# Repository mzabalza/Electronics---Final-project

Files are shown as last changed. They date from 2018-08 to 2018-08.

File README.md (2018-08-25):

# Electronics-Final_project
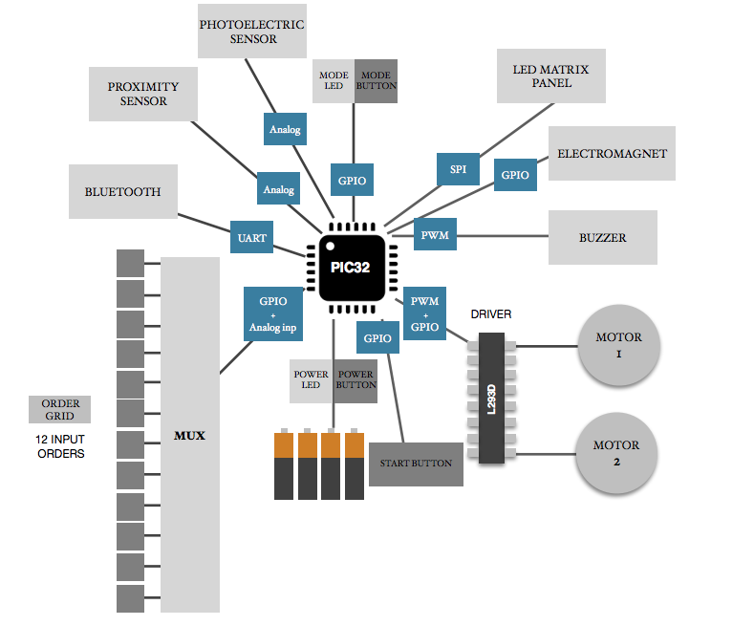
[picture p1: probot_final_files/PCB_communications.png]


## 1. Probot_final_files
- Project description pdf(Probot_memory_v4).
- Bill of materials (BOM).
- Datasheets of every electronic component.
- Gerber files.
- Altium schematics of project.

## 2. Test_components
- PIC32MX340F256H datasheet.
- C code programms of every functioanlity:
  - Motor driver
  - Mux
  - Proximity sensor
  - Bluetooth
  - LDR
  - Led Matrix

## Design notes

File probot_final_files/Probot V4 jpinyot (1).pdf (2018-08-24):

# 42 ELECTRONICS

# Technical Reference

Authors: Mikel Zabalza, Josep Pinyot, Jaume Garcia

08 03 2018

Version 1.4

# PROBOT

# CONTENTS

### 1 Introduction

### 2 Block Diagram

### 3 Instruction manual

### 4 Components

4.0 Component table
4.1 PIC32MX1
4.2 Proximity sensor
4.3 Photoelectric sensor
4.4 Order grid
4.5 Motor
4.5.1 Motor Driver
4.6 LED
4.7 Electromagnet
4.8 Display panel
4.9 Buzzer
4.10 Bluetooth
4.11 Battery
4.12 Mode Selector
4.13 Robot structure

### 5 Electric Consumption

### 6 Protocols

6.1 PWM
6.2 GPIO
6.3 SPI
6.4 UART
6.5 Motors
6.6 Analog

# 1. INTRODUCTION

Probot is a programable robot, able to make different moves and actions, Its an introduction to robotics and programming, making it more accessible for the youngest audience .This 2-wheel-driven robot is designed to be configured through visual programming.

## 1.1 MAIN UTILITIES

Perform a series of movements pre introduced by the user through an APP or through a physic panel using specific pieces that represent the movements: go forward, go backward, turn left and turn right. There will be too more specific pieces representing, velocity, performing time for a movement, reproduce sounds and degrees of turn.

Apart from the main utilities our project will be able to detect colours from the floor and detect collisions allowing the user create labyrinths himself for solve using the commands and treating the cases of collision and colour error as if the user would have failed, and it could take little metal objects too using an electromagnet.

It could save specific patrons in memory for perform complex and varied sets of movements.

The robot contains a led panel to be able to show the actual movements that it is performing among other esthetics things as messages, expresions, faces …

## 1.2 GOAL

The aim of this project is to make a toy in a computational thinking concept, So that its users can develop skills such us:

- Develop programs to complete certain tasks (go through a labyrinth, pick up objects…)
- Understand the execution of the selected program
- Learn through error and predict what a program will do.
- Evaluate and refine a simple program.

# 2. INSTRUCTION MANUAL

Probot is an introduction to robotics and programming for the youngest audience .The robot is designed to execute a set of action through an app, that communicates with the robot via bluetooth, and a grid of different pieces witch you can choose to run specific actions.

The user is able to change between the two possibles inputs with the “mode selection” button, through the colour of the LED the user will know the selected input (blue for bluetooth and red for the grid orders).

## 2.1 CONFIGURATION WITH THE GRID

The grid is the main part of Probot, it is located at the top of the robot to facilitate the interaction. To run Probot with the grid make sure the “mode selection” LED is red, if not the user can change from bluetooth to grid mode pressing the button next to it (the “mode selection” button).

Once Probot is set in grid mode, the user can place the set of piece he want to move the robot, thanks to the sensor located in front of the robot it will never crash.

The different pieces the user can use are:

GO FORDWARE: to make the robot move forward.

GO BACKWARDS: to make the robot move backwards.

TURN LEFT: to make the robot turn left.

TURN RIGHT: to make the robot turn right.

POWER IMAN: to power the electromagnet located down the robot.

STOP IMAN: to stop the electromagnet located down the robot.

POTENTIOMETER: this piece consist of a simple potentiometer, that the user can place it right after the command pieces to change some values of the action (for FORDWARE and BACKWARDS pieces will change the distance to travel and for TURN pieces will change the angel). Also the user can place one POTENTIOMETER in the first place of the grid to change the speed of all the actions.

GUIDE ME: this pieces is designed to help the youngest play with Probot, helped with the distance sensor Probot will set automatically the distance and the angle to avoid collision, when it moves and turns respectively.

## 2.2 CONFIGURATION WITH THE APP

To run Probot with the app make sure the “mode selection” LED is blue, if not the user can change from grid to bluetooth mode pressing the button next to it (the “mode selection” button).

The Probot app is a easy to use interface with similar options as the grid, the main different with the grid are the limited places were the user can place the pieces in the grid and the memory option.

The memory option is a interesting option when the user find a pattern of pieces that runs the robot without crashing. When the user wants to save a pattern he needs to press the “memory” button on the app, also the user will be able to name the pattern. When the user wants to recover the pattern he will need to press the “recover” button and select the wanted pattern from the menu.

### 2.3 INTERACTIVE PARTS

Probot will be able to interact directly with the user with the LED panel and the buzzer. Both are build not just to facility and improve the experience with the robot, also thous parts will hep the user to know interesting things about the patterns.

LED PANEL: It will help the user to know the step of his pattern the robot has crashed, showing the number of the piece.

PUZZER: The buzzer will help the user emitting sounds when it crash and a simple music when he found a pattern that runs the Probot without crashing.

# 3. BLOCK DIAGRAM

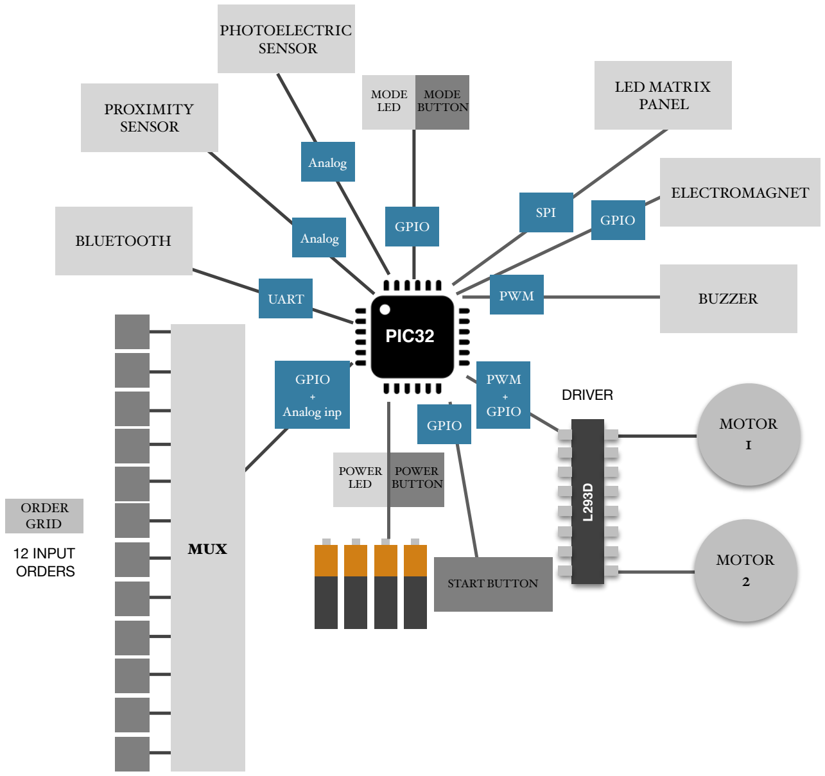
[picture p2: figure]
12 INPUT ORDERS; MOTOR 1; MOTOR 2; PIC32; DRIVER; ORDER GRID; BLUETOOTH; PROXIMITY SENSOR; BUZZER; LED MATRIX PANEL; POWER LED; UART; PWM +; GPIO; GPIO + Analog inp; POWER BUTTON; MODE LED; MODE BUTTON; MUX; START BUTTON; ELECTROMAGNET; PWM; SPI; Analog; PHOTOELECTRIC SENSOR

COMPONENT

PROTOCOL

# 4. COMPONENTS

## 4.1 COMPONENT TABLE

Component | Uds | Manufactu rer | M. Reference | Supplier | S. Reference | Price (EUR)
Microcontroller | 1 | Microchip | PIC32MX270F256 D-50I/PT | Farnell | 2449081 | 4.46
Proximity sensor | 1 | SHARP | GP2Y0A41SK0F | Farnell | 1618431 | 15
Female PIN sensor | 1 | Pololu | 3-Pin Female JST PH-style | Exp-tech | - | 0.82
Buzzer | 1 | Pro-signal | ABT-414-RC | Farnell | 2098836 | 1.55
Drive Motor | 1 | Texas Instruments | L293DNE | Farnell | 1470423 | 1.78
Analog MUX | 1 | Texas instruments | CD74HC4067SM96 | Farnell | 1601157 | 0.4
Led matrix | 1 | Kingbright | TA08-81GWA | Farnell | 2290396 | 6.15
Shift Register | 2 | Texas Instruments | CD74HC164M | Farnell | 1103161 | 0.589 x 2 = 1.17
Bluetooth module | 1 | MICROCHIP | RN4020-V/RM | Farnell | 2442930 | 9,38
Photoelectric sensor | 1 | ADVANCED PHOTONIX | NORPS-12 | Farnell | 327700 | 3.18
Potentiometer | 1 | BOURNS | 3362P-1-103LF | Farnell | 9354391 | 1
Mode Switch | 2 | NKK switches | SS12SDP2 | Farnell | 1524325 | 0.05 x 2 = 0.1

## 4.1 MICROCONTROLLER

PIC32MX270F256D-50I/PT

Fabr. Ref | PIC32MX270F256D-50I/PT
Farnell Code | 2449081
Frecuency: | 50MHz
Pins: | 44 where 34 are I/O.
Interfaces: | UART, SPI, I²C, I²S, USB
RAM: | 64KB
Memory size: | 256KB
Consume (50 Mhz) | 25mA
USED PINS

USED PINS:

I = Input | O = Output | CO = Compare Output
CONNECTED COMPONENT | PIN | FUNCTION
POWER | 1 | RB9 – I
MODE | 2, 3, 4 | RC6 – I/ RC7 – O/ RC8 – I
GRID ON | 5 | RC9 – O
PROXIMITY SENSOR | 11 | AN11 – I
GRID | 36, 30, 31, 32, 33, 34 | AN12 — I / RA2 — O / RA3 — O / RA8 — O / RB4 — O / RA4 — O
DECODER GRID | 8, 9 | RB10 – O / RB11 – O
MTR DRIV PULSE | 19, 20 | RPA0 – CO / RPA1 – CO
MTR DRIV MTR1 | 21, 22 | RB0 – O/ RB1 – O
MTR DRIV MTR2 | 23, 24 | RB2 – O/ RB3 – O
ELECTROMAGNET | 27 | RC2 — O
MATRIX LED | 14, 41, 43, 44 | SCK / RPB5 — SPI / RPB7 — SPI / RPB8 — SPI
BUZZER | 15 | RPB15 – CO
BLUETOOTH | 12, 13, 25, 26 | RA10 – O / RA7 – O / RPC0 – Rx / RPC1 – Tx

### 4.2 PROXIMITY SENSOR

The infrared proximity sensor will detect how far away an object is, the PIC32 micro controller will interpret the input and generate an order. Example: stop the motors before hitting an obstacle.

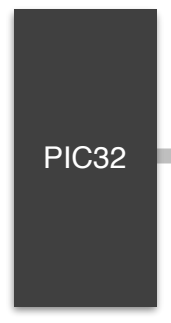
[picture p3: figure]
PIC32

The sensor will output an analog voltage depending how far away an object is from the sensor. It will be connected to the micro controller using the Analog to Digital converter pin.

SNS-US020 Ultrasonic Sensor

- Manufacturer SHARP
- Supplier Farnell
- Manufacturer Reference GP2Y0A41SK0F
- Supplier Reference 1618431
- Range 4 to 30cm
- Power supply 4.5 to 5.5 V
- Analog voltage output 0.4V
- Consumption 30 mA
- Price 7.8 EUR

The sensor needs a 3 pin adapter to be able to connect it to the PCB.

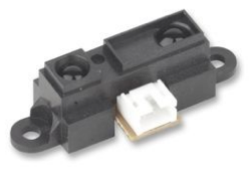
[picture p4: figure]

The 3-Pin Female JST PH-Style Cable has been selected for this purpose

3-Pin Female JST PH-Style Cable

- Manufacturer Pololu
- Supplier exp-tech
- Price 0.82 EUR

RA0/VA0

+5V

Vo | Vcc
OUT

GND

The graphic below taken from the data sheet shows how the voltage output from the sensors varies with the distance detected. With distances below 4cm we could get repeated voltages and above 30 cm, they are not conclusive.
Considering this we will able to assign the different voltage inputs between 0, 4 and 3 V to its corresponding distance, in our PIC32. However we will set 0 and 5V as reference voltages. The digital value is calculated based on following equation.

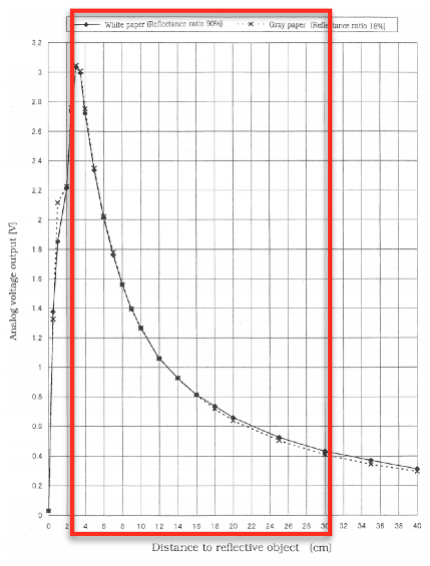
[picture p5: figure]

Interfacing to the microcontrollers is straightforward. The sensor will output a single analog output voltage (OUT) connected to an analog-to-digital converter for taking distance measurements. The 10-bit ADC pin of the PIC provides readings from 0 to 1023 as the input voltage rises from 0 to Vdd (5V).
The sensor automatically updates the output approximately every 16 ms.

### 4.3 PHOTOELECTRIC SENSOR

The LDR will be used with a RGB LED to detect colours. Measuring the LED’s light reflected in the surface we want measure having like that 3 measures one for RED, another for GREEN and one last for BLUE, with those three measures we can determinate a colour.

For the LDR one side of the sensor will be connected to the power supply while the other will be connected to an analogical input pin of the microcontroller. The analog input will be connected to a pull-down resistor to ground.

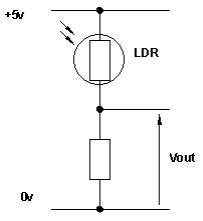
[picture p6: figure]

we will use the model LDR CdS PHOTO CELL from Farnell with the specifications:

LDR CdS PHOTO CELL

- Manufacturer ADVANCED PHOTONIX
- Supplier Farnell
- Supplier Reference NORPS’12
- Supplier Reference 327700
- Darkness resistance 1 Mohm
- Darkness resistance 100 Kohm

RGB LED

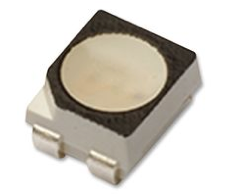
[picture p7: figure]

- Manufacturer BROADCOM LIMITED
- Supplier Farnell
- Supplier Reference ASMB-MTB0-0A3A2
- Supplier Reference 2401105
- Direct Tension R 2.1V / G 3.1V / B 3.1V
- Direct Current R 20mA / G 20mA / B 20mA

For the RGB LED we have 4 pins:

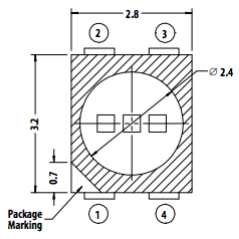
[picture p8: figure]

The anode will be connected to GND and the others connected to a resistor and a digital pin.

### 4.4 ORDER GRID

As explained in the instruction manual, the robot could be programmed plugging some pieces directly into the car. So the car is going to have 16 holes available for 10 different types of pieces(each piece representing an order, such us, go straight/backwards, turn left-right, activate magnet…). A 16-Channel Analog Multiplexer has been selected to connect 16 inputs of the order grid with the micro controller.

The multiplexer is a combinational circuit device that selects one of N inputs and provides it on its output. We can determine which input should be passed to the output trough a number of digital inputs called select lines. If there are n select lines, then the maximum input lines are 2^n.
In this case, with a multiplexer of 16 analog inputs we need 4 select lines. The 4 select lines will be General-purpose input/output (GPIO), configured as digital outputs from our PIC32. The figure below shows how the combination of all 4 select lines will allow us to select the desired analog output (L= Low, H = High):

The selected multiplexer has also an ENABLE input, which has to to be activated to perform the multiplexer operation. This will be also an general purpose input/output (GPIO) from the PIC32. This integrated circuit has active LOW ENABLE and the 4 select lines as input and gives complementary outputs.

S1 INPUT | S2 INPUT | S3 INPUT | S4 INPUT | E ENABLE | OUTPUT
L | L | L | L | L | D0
L | L | L | H | L | D1
L | L | H | L | L | D2
L | L | H | H | L | D3
L | H | L | L | L | D4
L | H | L | H | L | D5
L | H | H | L | L | D6
L | H | H | H | L | D7
H | L | L | L | L | D8
H | L | L | H | L | D9
H | L | H | L | L | D10
H | L | H | H | L | D11
H | H | L | L | L | D12
H | H | L | H | L | D13
H | H | H | L | L | D14
H | H | H | H | L | D15

The image below shows the scheme of the input grid - mix - PIC32. The order pieces are represented with the green boxes.

un

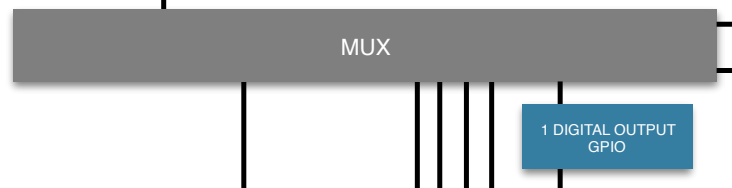
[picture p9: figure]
MUX; 1 DIGITAL OUTPUT GPIO

This is the selected MUX:

16 :1 Analog Multiplexer

- Manufacturer TEXAS INSTRUMENTS
- Supplier Farnell
- Manufacturer Reference CD74HC4067SM96
- Supplier Reference 1601157
- Power supply 2 to 6 V
- PINS 24

The Analog input received by the PIC32 will be a voltage value between 0 and 3.3 V. The PIC receive this input through its 10 - bit analog to digital conversion input (ADC). This pin is able to read 1024 different values between voltage 0 and 3.3 V. In this project there will be just 10 different cases, representing 10 different inputs (10 different R2).

ANALOG
INPUT (ADC)

4 DIGITAL OUTPUT
GPIO

+5V

Vcc

Gnd

Selecting a value of R1 (50 Ohm) and combining different input values of R2, we obtain different voltage outputs, as it is shown in the table bellow.

V = R x I
R = R1 + R2

I = V/(R1 + R2)
I = 5/(50 + R2)

V2 = V1 - (R1 x I)
V2 = 5 - (R1 x I)

The first order will be reserved for the potentiometerter order piece. For this, we will use a 10 Ohm potentiometer which will allow us to reserve the range between 0 and 0,83 V for this utility.

3362P-1-103LF Potentiometer
- Fabricant Bourns
- Fabricant Ref 3362P-1-103LF
- Supplier Farnell
- Supplier Ref 9354301
- Resitance 10 Ohms
- Clock Frecuence 30Mhz
V1(V) | 5
R1(Ohm) | 10000
| R2 order x (Ohm) | I (A) | V2 (V)
R2 Potentiometer | 700 | 0,00047 | 0,33
R2 order 2 | 1500 | 0,00043 | 0,65
R2 order 3 | 2800 | 0,00039 | 1,09
R2 order 4 | 4000 | 0,00036 | 1,43
R2 order 5 | 5500 | 0,00032 | 1,77
R2 order 6 | 7000 | 0,00029 | 2,06
R2 order 7 | 9000 | 0,00026 | 2,37
R2 order 8 | 12000 | 0,00023 | 2,73
R2 order 9 | 15000 | 0,00020 | 3,00
R2 order 10 | 20000 | 0,00017 | 3,33

+5V

I

V2

R1

R2

### 4.5 MOTOR

The motor is the output element, responsible of the robots 4 basic movements: Forward, Backward, left turning, right turning. Two motors respectively connected to independent wheels, will be enough for this. This are the main characteristics of the selected motors:

MOTOR MG-6-120

- Supplier Olimex
- Supplier Reference MG-6-120
- Double shaft Gear Motor
- Voltage 3 - 6 VDC
- Current < 300 mA
- Speed 100 rpm
- Torque 1.0 kgf.cm
- Price 2.5 EUR

The motors can not be controlled directly from the micro controller pin. Thus we need a motor controller.

4.5.1 MOTOR DRIVER

The motors will be controlled through the motor driver L293D:

MOTOR DRIVER L

- Manufacturer Texas Instruments
- Manufacturer Reference L293DNE
- Supplier Farnell
- Supplier Reference 1470423
- Supply Voltage min/max (Motor Voltage) 4.6/36V
- Output Voltage 39V
- Maximum Continuous Motor Current 600mA
- Output Current 1.2A
- Nº Pins 16
- Price 1.784 EUR

The L293D is a 16-Pin Motor Driver IC, capable of running two DC motors at any direction at the same time. The Driver works on the principle of Half h-Bridge, which is a set up used to run motors both in clock and anti clockwise direction. A PWM signal from the PIC will tell the power transistor when to turn the motor on and when to turn the motor off. The PWM’s duty cycle will determine the speed the motor turns.

This schema together with the table below, summarizes the connection between the PIC, the motor Driver, and the two motors

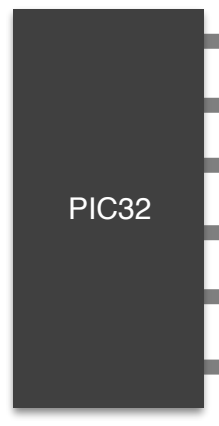
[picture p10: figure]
PIC32

PIN | DESCRIPTION | PIN | DESCRIPTION
1 | Control of Voltage supplied to the motor. PWM signal | 9 | Control of Voltage supplied to the motor. PWM signal
2 | Control of the direction of the motor rotation | 10 | Control of the direction of the motor rotation
3 | Motor 1 | 11 | Motor 2
4 | Ground pins connected to ground of circuit (0V) | 12 | Ground pins connected to ground of circuit (0V)
5 | Ground pins connected to ground of circuit (0V) | 13 | Ground pins connected to ground of circuit (0V)
6 | Motor 1 | 14 | Motor 2
7 | Control of the direction of the motor rotation | 15 | Control of the direction of the motor rotation
8 | Motor Voltage supply | 16 | Circuit Voltage supply (5V)

Vcc
PWM
M2

1 2 3 4 5 6 7 8

16 15 14 13 12 11 10 9

PWM
M1 | Vmotor

digital signal

digital
signal

digital
signal

digital signal

PWM Motor 1

I/O Motor 1

I/O Motor 1

PWM Motor 2

I/O Motor 2

I/O Motor 2

PWM Pulse-Width Modulation I/O Digital Input/Output

### 4.6 ELECTROMAGNET

To drive the electromagnet we will need more than 3V, for that reason we will use one Mosfet transistor with the gate connected to the PIC32, the source connected to ground and the drain connected to the ground connection of the electromagnet. The electromagnet will go connected to the battery directly.

As we didn’t found a electromagnet that meets our requirements, we will buy a relay to disassemble and collect the coil to use it our project as our electromagnet.

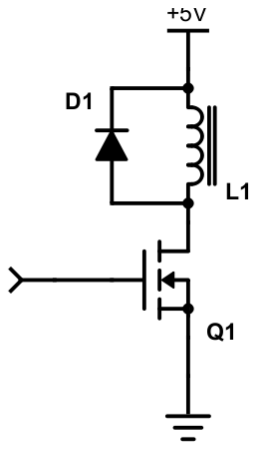
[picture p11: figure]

### Mosfet transistors 2N7002

- Manufacturer Microchip
- Manufacturer Reference 2N7002-G
- Supplier Farnell
- Supplier Reference 2775064
- Transistor polarity N-channel
- Price 0.175 EUR

### Standard Recovery Diode

- Manufacturer Multicomp
- Manufacturer Reference 1N4001
- Supplier Farnell
- Supplier Reference 9564993
- Repetitive Reverse Voltage 50V
- Forward Voltage VF Max 1.1V
- Price 0.07 EUR

### Signal relay

- Manufacturer AXICOM
- Manufacturer Reference IM03NS
- Supplier Farnell
- Supplier Reference 1770584
- Coil Voltage 5V
- Price 1.66 EUR
PROTOCOL | DESCRIPTION
GPIO | This port will be connected to the transistor in order to power the electromagnet.

### 4.8 LED MATRIX

Our LED matrix works on the principle of multiplexing. The PIC32 is connected to the shift register and sends the data and the clock by different lines .

LED Dot Matrix

- Manufacturer Kingbright
- Manufacturer Reference TA08-81GWA
- Supplier Farnell
- Supplier Reference 2290396
- LED color Green
- Supply Voltage 2.2V
- Display Dots x Lines 8x8
- Price 6.15 EUR

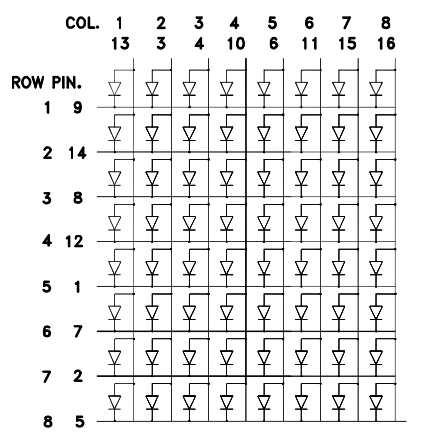
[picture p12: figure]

### 4.8.1 SHIFT REGISTER

To power our LED matrix we will use two 8-bits shift registers (serial-in, parael-out), connecting the outputs of one of them direct to the rows(positive), and the outputs of the other connected to mosfet transistor(with source connected to ground and drain to the column of the LED).

### Shift Register 74HC164

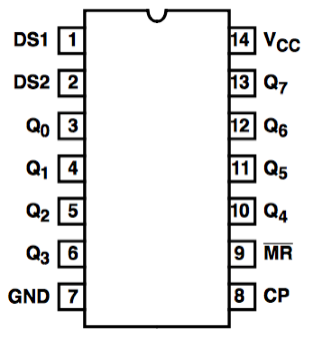
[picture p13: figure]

- Manufacturer Texas Instruments
- Manufacturer Reference CD74HC164M
- Supplier Farnell
- Supplier Reference 1103161
- Supply Voltage min/max 2/6V
- Nº Pins 14
- Nº of Bits Per Element 8bit (http://uk.farnell.com/w/c/semiconductors-ics/logic/shift-registers?no-of-bits-per-element=8bit)
- Price 0.58 EUR

### Mosfet transistors 2N7002

- Manufacturer Microchip
- Manufacturer Reference 2N7002-G
- Supplier Farnell
- Supplier Reference 2775064
- Transistor polarity N-channel
- Price 0.175 EUR

### 4.9 BUZZER

The buzzer is one of our output elements build to ease the interaction with the device. To control the buzzer we will connect the output from the PIC32 to the gate of one Mosfet transistor, with source connected to ground and the drain connected to the output of the buzzer. In this way we will be able to run the buzzer with more voltage than using the output of the PIC32.

To prevent the PIC32 and the transistor of suffering back-emf, we will put a suppression diode across the buzzer.

To generate an audio signal to play on the buzzer we will set the PWM period to 1/frequency of the desired sound, So we can generate different frequencies.

### Buzzer

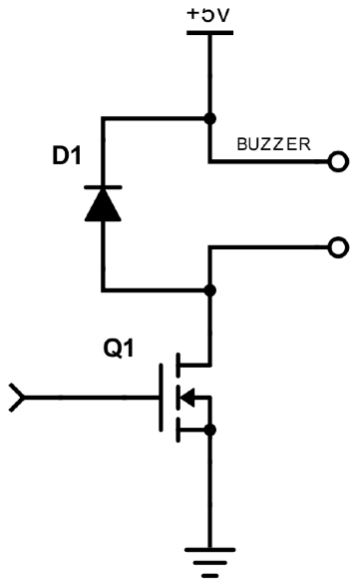
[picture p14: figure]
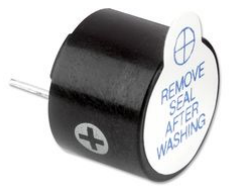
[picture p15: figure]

- Manufacturer Pro-signal
- Manufacturer Reference ABT-414-RC
- Supplier Farnell
- Supplier Reference 2098836
- Supply Voltage Min/Max 3/8V
- Sound Level SPL 85dB
- Price 1.55 EUR

Mosfet transistors 2N7002

- Manufacturer Microchip
- Manufacturer Reference 2N7002-G
- Supplier Farnell
- Supplier Reference 2775064
- Transistor polarity N-channel
- Price 0.175 EUR

### Standard Recovery Diode

- Manufacturer Multicomp
- Manufacturer Reference 1N4001
- Supplier Farnell
- Supplier Reference 9564993
- Repetitive Reverse Voltage 50V
- Forward Voltage VF Max 1.1V
- Price 0.07 EUR
PROTOCOL | DESCRIPTION
PWM | This output will be connected to the transistor in order to control the frequency we want to reproduce, but also to turn on and off the sound.

### 4.10 BLUETOOTH

For our bluetooth communication we have chosen a low energy Bluetooth module RN4020 by Microchip. Using this module we can receive and send information from our PIC to a mobile application or a computer. The communication between PIC and RN4020 are established through one of the UART modules present in our PIC.

The WAKE_HW and WAKE_SW pins of the bluetooth module control the sleep, activation and reset modes of the module. The c

### BLUETOOTH MODULE RN4020

- Operating Voltage 3.3V
- Input Power Supply 3.6V - 6V
- Frequency Band 2.4GHz 2. 48GHz
- Internal flash memory 64KB
- Price 9.38

PIC32

VCC
Gnu
TX
RX
WAKE-HW
WAKE_SW

Modulo Bluetooth RN4020

### 4.11 BATTERY

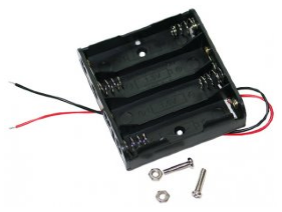
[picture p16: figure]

The voltage will be supplied to the circuit through four A4 batteries connected in series. This way 5V will be supplied using rechargeable A4 batteries.
However, as our PIC32 operates in 3.3V . A voltage regulator will be added between the battery and the PIC voltage input to get the desired voltage.

The output of the battery will directly connected to a switch witch allow to have a direct control to to entire circuit and this one will be connected to to the voltage regulator
We will use a TPSM84203EAB voltage regulator following the next connection schema:

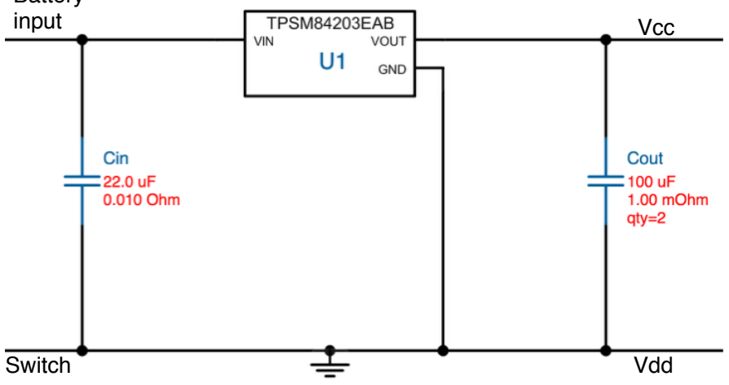
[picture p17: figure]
Vcc; Switch; Vdd; input

### Voltage regulator

## PIC32

Battery

- Manufacturer TEXAS INSTRUMENTS
- Manufacturer Reference LMR14203XMKE/NOPB
- Supplier Farnell
- Supplier Reference 2323516
- Input Voltage Min/Max 4.5V / 42V
- Output Voltage Min/Max 0.765V / 34V
- Output Max Corrent 0.3A
- Price 2.76 EUR

### Capacitator Cout

- Manufacturer MURATA
- Manufacturer Reference GRM31CR61A226KE19L
- Supplier Farnell
- Supplier Reference 1907515
- Tension Nominal 10V
- Capacitance 22µF
- Price 0.783 EUR
- Quantity 2

### Capacitator Cin

- Manufacturer TDK
- Manufacturer Reference C1005X6S1C105K050BC
- Supplier Farnell
- Supplier Reference 2525035
- Tension Nominal 16V
- Capacitance 1µF
- Price 0.136 EUR

### Capacitator Cboot

- Manufacturer MURATA
- Manufacturer Reference GRM188R71A224KA01D
- Supplier Farnell
- Supplier Reference 1828889
- Tension Nominal 16V
- Capacitance 0.22µF
- Price 0.12 EUR

### Diode

- Manufacturer DIODES INC.
- Manufacturer Reference ZLLS410TA
- Supplier Farnell
- Supplier Reference 1843764
- Direct Corrent 750mA
- Direct Max Tension 580mV
- Price 0.373 EUR

### Inductor

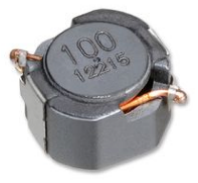
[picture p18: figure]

- Manufacturer TDK.
- Manufacturer Reference CLF6045T-680M
- Supplier Farnell
- Supplier Reference 2360936
- Saturation Corrent 790mA
- Price 0.942 EUR

### Resistor Rfb2

- Manufacturer VISHAY
- Manufacturer Reference CRCW04023K32FKED
- Supplier Farnell
- Supplier Reference 1652792
- Tension Nominal 50V
- Potence Nominal 63mW
- Resistance 3.32kohm
- Price 0.0573 EUR

### Resistor Rfb1

- Manufacturer PANASONIC ELECTRONIC COMPONENTS
- Manufacturer Reference ERJ2RKF1021X
- Supplier Farnell
- Supplier Reference 2302641
- Tension Nominal 50V
- Potence Nominal 100mW
- Resistance 1.02kohm
- Price 0.0269 EUR

### SWITCH

- Manufacturer NKKswitches
- Manufacturer Reference SS12SDP2
- Supplier Farnell
- Supplier Reference 1524325
- Price 1.63 EUR

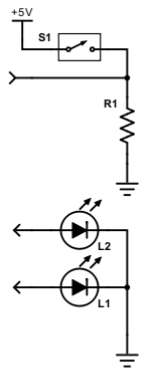
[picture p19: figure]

### 4.12 MODE SELECTOR

We decide to implement a simple button to be able to change from grid to bluetooth mode, also we have implement a two colour LED to indicate the mode we are working in.

We will connect the input of the switch to our 5V source, and the output connected to a Pull Down resistance connected to ground. Between the resistance and the switch we will connect our PIC input.
The two LEDs will be connected each one to different outputs of the PIC to indicate in witch mode are the user working in.

LED Blue

- Manufacturer Multicomp
- Manufacturer Reference MCL053SBLC
- Supplier Farnell
- Supplier Reference 1581185
- LED color Blue
- Supply Voltage 3.6V
- Current 20mAh
- Luminous Intensity 2.500 mcd
- Price 0.379 EUR

LED Blue

- Manufacturer Rafi
- Manufacturer Reference 1.90.690.295/0000
- Supplier Farnell
- Supplier Reference 9929509
- LED color White
- Supply Voltage 3.6V
- Current 20mAh
- Luminous Intensity 2.500 mcd
- Price 0.379 EUR

### Resistencia SMD de Tipo Chip

- Manufacturer Electronics
- Manufacturer Reference LR1206-R07FW
- Supplier Farnell
- Supplier Reference 1100335
- Resistance 0.07 ohm
- Price 0.546 EUR

### SWITCH

- Manufacturer NKKswitches
- Manufacturer Reference SS12SDP2
- Supplier Farnell
- Supplier Reference 1524325
- Price 1.63 EUR
PROTOCOL | DESCRIPTION
GPIO IN | This PIC pin will be connected to one of the pins of the switch and it will be connected to the battery. In this way we will use the LOW state of the port to set on mode and the HIGHT to the other mode (grid/bluetooth).
GPIO OUT | It will power one of the LEDs.
GPIO OUT | It will power one of the LEDs.

### 4.13 START BUTTON

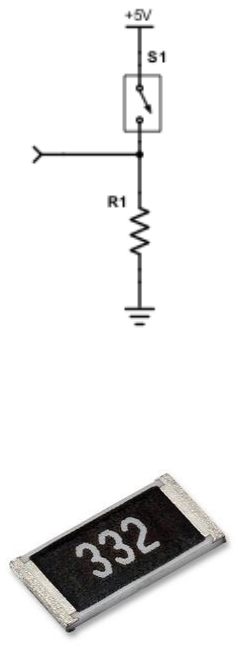
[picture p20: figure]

With this button we will be able to send a signal when the user wants the robot to begin to obey the grid orders.

We will connect the input of the switch to our 5V source, and the output connected to a Pull Down resistance connected to ground. Between the resistance and the switch we will connect our PIC input.

### Resistencia SMD de Tipo Chip

- Manufacturer Electronics
- Manufacturer Reference LR1206-R07FW
- Supplier Farnell
- Supplier Reference 1100335
- Resistance 0.07 ohm
- Price 0.546 EUR

### SWITCH

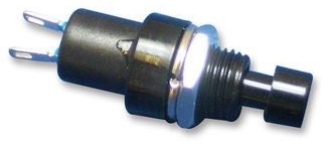
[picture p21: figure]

- Manufacturer Multicomp
- Manufacturer Reference R13-509A-05-BB
- Supplier Farnell
- Supplier Reference 1634682
- Price 1.42 EUR

### 4.14 MAIN ROBOT STRUCTURE

### WHEELS

- Supplier OLIMEX
- W1 Supplier Reference MG-WHEEL
- W2 Supplier Reference ROBOT-CW
- Price 3 X 1 = 3 EUR

### CHASIS

- Supplier OLIMEX
- Supplier Reference ROBOT-CHASSIS-4
- Price 4 EUR

### BATTERY HOLDER

- Supplier OLIMEX
- Supplier Reference BAT-HOLDER-4XAA
- Price 0.5 EUR

### 5 ELECTRICAL CONSUMPTION

With an average use of Probot (that means do not push the motors to the maxim power) and using as much devices as possible the calculations for the autonomy would be the next ones:

With a 900mA battery we will have an autonomy of:

900/757= 1 hora 10 min

In terms the power:

COMPONENT | AVERAGE CONSUMPTION
Proximity Sensor | 12 mAh
Motor | ~300 x 2 = 600 mAh
LED Mode | 20 mAh
LED RGB | 20 mAh
LED Power | 20 mAh
LED Matrix ( 1 LED at a time) | 20 mAh
Buzzer | 40 mAh
PIC | 25 mAh

757 mAh

COMPONENT | | AVERAGE POWER
Proximity sensor | 12 mA x 5V | 0.06W
Motors | 300 mA x 2 x 5V | 3W
LEDs | 20 mA x 4 x 3V | 0.24W
Buzzer | 40 mA x 5V | 0.2W
PIC | 25 mA x 3.3 | 7.57W

### 11 W

### 6 PROTOCOLS

### 6.1 PWM

The pulse-width modulation (PWM) is a analog protocol that use modulation technique to encode a message into a pulsing signal, this method can be used to transmit information or to control the voltage sent. With PWM we can change the width of the pulse without changing the frequency.

The average value of voltage and current at the output is controlled with the duty cycle, the fraction of one period in which a signal is active, and with the modulation frequency, how many times the pulse went ON and OFF. A low duty cycle corresponds to low power, because the power is off for most of the time.

The main advantage of PWM is the low power loss. When a switch is off there is practically no current, and when it is on and power is being transferred to the load.

BUZZER

We decide to use PWM to be able to control the the output frequency of the buzzer with the frequency of modulation. We will set the PWM period to 1/frequency of the desired sound with a fixed duty cycle(50%,the buzzer will oscillate at its maximum amplitude), to have different sounds with the same volume.

To create a La4 (440 Hz) we will set the duty cycle to 50% and
the modulation frequency to 440 Hz. Each second will output 440 pulses of 50% of the pulse ON and 50% of the pulse OFF.
PIC | SHIFT REGISTER | DESCRIPTION
SPI | MR | RESET
SCK | CP | CLOCK
SPI | DS1 | DATA
SPI | DS2 | ENABLE

### 6.2 GPIO

General-purpose input/output (GPIO) is a generic pin of one integrated circuit, including whether it is an input or output pin is controllable by the user at run time. It is a rudimentary form of communication where you manually (in code) turn a pin on and off or read its state.

GPIO capabilities may include:
-GPIO pins can be configured to be input or output.
-GPIO pins can be enabled/disabled.
-Input values are readable (typically high or low).
-Output values are writable/readable.
-Input values can often be used as IRQs (typically for wakeup events).

MODE SELECTOR

For this parts we will need three GPIO ports, two outputs and one input. The input will be connected to the switch and will read HIGH or LOW, the two output will be connected to one of the LEDs each.

When input reads LOW, because the switch is off, it will set the robot as GRID mode and will send HIGH to the first output(GRID), and disable the second output(BLUETOOTH). On the contrary when input reads HIGH, because the switch is on, it will set the robot as BLUETOOTH mode and will send HIGH to the second output(BLUETOOTH), and disable the first output(grid).

ELECTROMAGNET

We will set one GPIO pin to output to be able to control the electromagnet, sending HIGH we will enable the electromagnet and we will turn it off disabling the output.

STAR BUTTON

This part have a simple functioning, when the button is pulsed the current flows to a GPIO port set as an input. When the GPIO input reads HIGH the robot will begin to obey the grid orders.

### 6.3 SPI

Serial Peripheral Interface (SPI) is an interface bus commonly used to send data between microcontrollers and small peripherals such as shift registers, sensors, and SD cards. It uses separate clock and data lines, along with a select line to choose the device you wish to talk to.

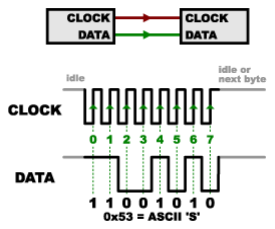
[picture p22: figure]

SPI is a synchronous protocol, which means that it uses
separate lines for data and clock, that keeps both sides in
perfect sync. The clock is an oscillating signal that tells the receiver exactly when to sample the bits on the data line, could be the rising or falling edge of the clock signal.

As we can see in the image when the clock pin receive the rising edge checks the state on the data pin. In this we will have the next binary code: 11001010.

Advantages of SPI:
-It’s faster than asynchronous serial.
-The receive hardware can be a simple shift register. -It supports multiple slaves.

Disadvantages of SPI:
-It requires more signal lines.
-The communications must be well-defined in advance.

LED MATRIX

To power our LED matrix we will use two 8-bits shift registers (serial-in, parael-out), connecting the output of one of them direct to the rows(positive), and the outputs of the other connected to mosfet transistor(with source connected to ground and drain to the column of the LED).

We will use this system to enable one column at a time to take advantage of a human eye problem, that maintains the image of the view for about 20 or 30 milliseconds.
With the column shift register we will enable one output at a time, but with the row shift register we will need enable up to the 8 outputs.

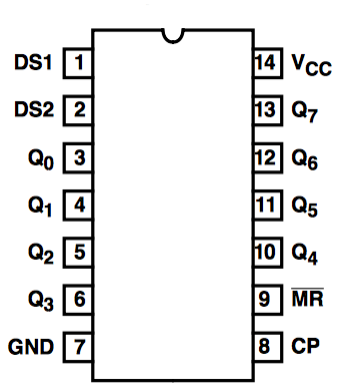
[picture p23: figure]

Connections:
Because we have two shift registers that need to work together,
we will connect the MR, CP and DS2 ports of both shift registers in parallel to the same pins on the PIC.

With the CLOCK input we will receive a regular signal to indicate, in the raising edge, where to read the value in the DATA input.
The DATA input will read a 8 bits(8 raises of the edge of the CLOCK) signal, each of thous bits correspond to a one of the different output. For example to turn on the row number 2, 6, 7 of the column 3 we will send 00100011 to the X edge shift register and 00010000 to the Y edge shift register where 0 is LOW and 1 is HIGH. After receiving the 8 bits signal all the outputs will have memorised their status and sending a HIGH state with the ENABLE input we will enable the selected outputs.
With the RESET input we will have a LOW value when we want to change the memory of the outputs, otherwise the RESET input will recite always a HIGH value.

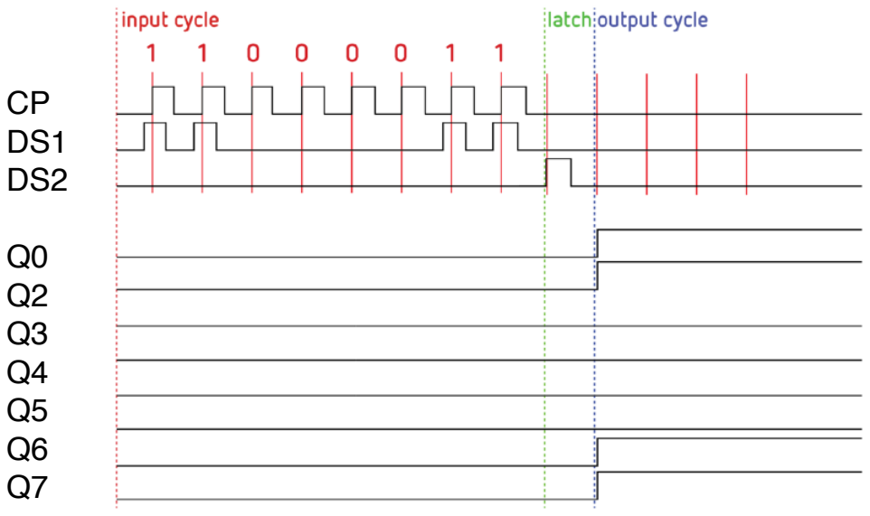
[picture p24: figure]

### 6.4 UART

We will use UART for implement the Bluetooth mode.

All the information we will send from our APP to UART module will agree this schema.

We will operate under 9600bps, 1 start bit, no parity bit, 1 stop bit and we will use 8 bits whose will be used for save a code to perform the desired actions.

The code we will use to communicate APP and PIC will be the next one:

We will use one bit for determinate wich components we will use. As we have 6 devices we will send as first package 8 bits where bits 0- 5 design usable devices and movement general specs: move forward or backward and turn left or right. And finally two more packages one package specificatin a number from 0 to 360² for turn angle and another package specificating a number from 0 to 100³ representing a percent of velocity.

1ºPackage: General INFO

bit 0 : MOTORS
bit 1 : (IF bit 0) 1 FORWARD 0 BACKWARD bit 2 : (IF bit 0) TURN LEFT¹
bit 3 : (IF bit 0) TURN RIGHT¹
bit 4 : LDR
bit 5 : PROXIMITY SENSOR
bit 6 : ELECTROMAGNET
bit 7 : BUZZER
bit 8 : LED MATRIX

2ºPackage Motor Turn Angle²

0 | 0 | 0 | 0 | 0 | 0 | 0 | 0 | 0 | = | 0
1 | 0 | 1 | 1 | 0 | 1 | 0 | 0 | 0 | = | 360

3ºPackage Motor Velocity³
0 | 0 | 0 | 0 | 0 | 0 | 0 | 0 | 0 | = | 0%
0 | 0 | 1 | 1 | 0 | 0 | 1 | 0 | 0 | = | 100%

NOTE ¹: if bit 2 and bit 3 are on the behaveur is undefined
NOTE ²: Specific a number greater than 360 will be in a undefined behaveur
NOTE ³: The cap will be blocked to 100 for prevent dangerous velocities

### 6.5 MOTORS

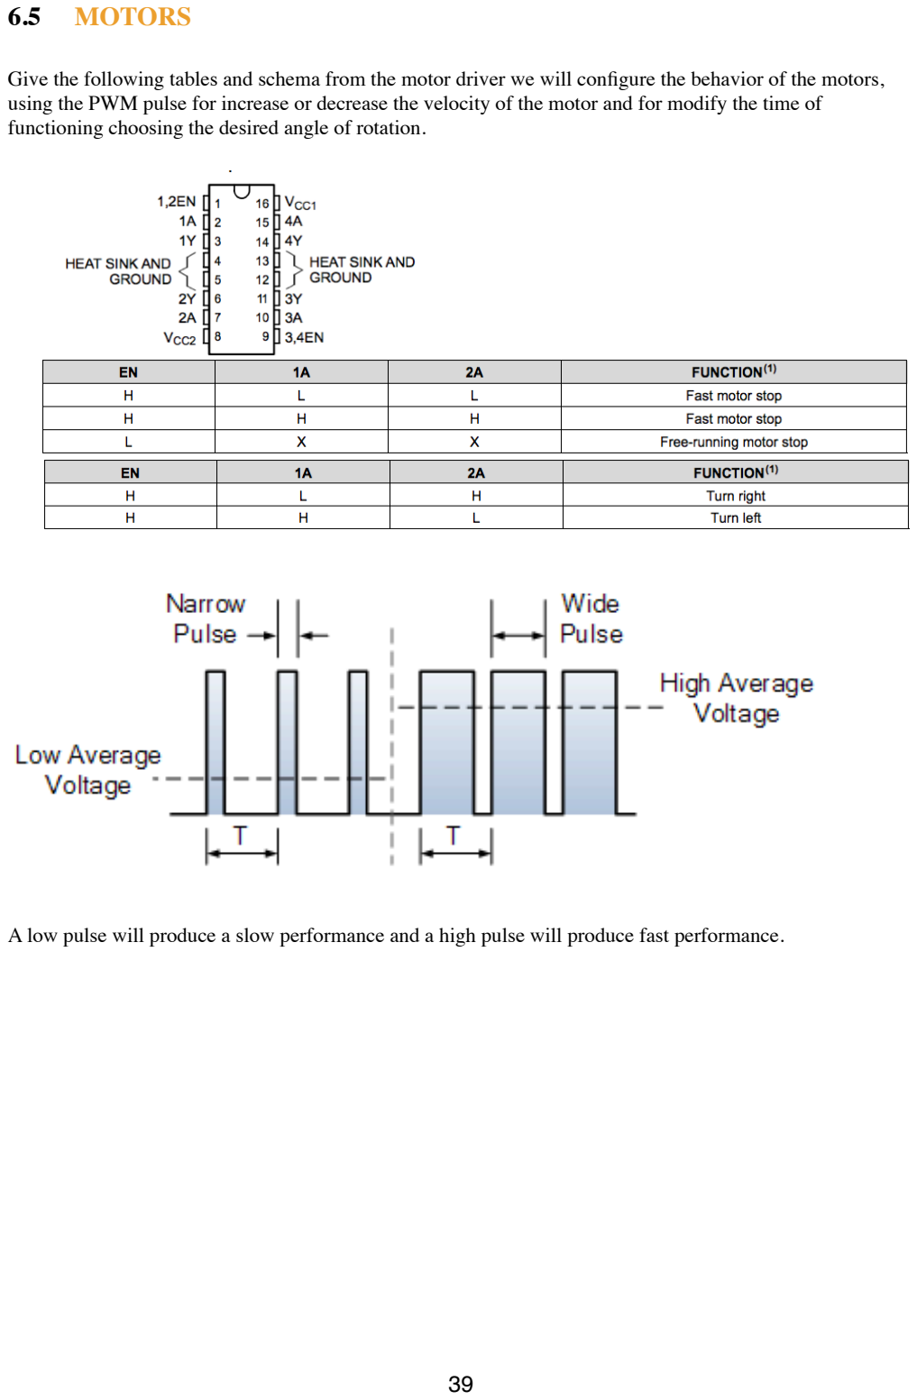
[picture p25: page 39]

Give the following tables and schema from the motor driver we will configure the behavior of the motors, using the PWM pulse for increase or decrease the velocity of the motor and for modify the time of functioning choosing the desired angle of rotation.

A low pulse will produce a slow performance and a high pulse will produce fast performance.

### 6.6 ANALOG TO DIGITAL CONVERTER (ADC)

Analog to Digital Converter (ADC) is used to convert analog signal-voltage into its equivalent digital number so that the micro controller can process that number.

The main feature of ADC signal is the resolution. The resolution indicates the possible number of digital values that can be converted from an analog input. Our micro controller has in-built 10-bit ADC, this means the digital value received lies between the range 0 to 1023. As the ADC range is 0 - 3.3V we will get a step size of 3.3V-2^10 = 3.23 mV.

In the case of proximity sensor we will set different outputs depending the distance to the obstacle. Some values will stop the robot while others will simply reduce its speed. In the case of the input grid we 10 different type of orders, meaning we can get 10 different analog input comping from our multiplexor. Thus the 10 - bit ADC its more than suitable for this purpose.

We can use the triangle method to find the binary representation of an analog input voltage. For example if we get a 2V input from the proximity sensor we will get (1024 x 2V)/5V = 410 V.
The analog input voltage of 2V will be represented by the binary number 110011010.

ADC

ANALOG SIGNAL | DIGITAL SIGNAL

### 6.7 PHOTOELECTRIC SENSOR

The LDR will be connected to an analog input pin for measure the voltage of the LDR, meanwhile the LED RGB will be connected to a 3 digital output pins, we will measure the LDR three times, one with RED ON, other with GREEN ON and another with BLUE ON. Due to LDR functioning the voltage will be different with the three inputs and we could measure the RGB intensity in each colour being able to detect colours.

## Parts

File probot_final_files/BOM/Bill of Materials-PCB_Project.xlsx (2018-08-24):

Quantity | Designator | Comment | Footprint | Description | Farnell Reference | Olimex Reference | LibRef
1 | C3 | Cap | Capacitor | Capacitor |  |  | Cap
1 | C4 |  | Capacitor | Capacitor |  |  | Cap
9 | C5, C6, C7, C8, C9, C15, C16, C17, C18 | 0.1µF | Capacitor | Capacitor |  |  | Cap
1 | C10 | 47 µF | Capacitor | Capacitor |  |  | Cap
1 | C11 | 220 nF | Capacitor | Capacitor |  |  | Cap
1 | C12 | 1 µF | Capacitor | Capacitor |  |  | Cap
1 | C13 | 1uF | Capacitor | Capacitor |  |  | Cap
1 | C14 | 100nF | Capacitor | Capacitor |  |  | Cap
1 | D1 | 1N4001 | Diode | Default Diode | 9564993 |  | Diode
3 | D2, D9, D11 | MCL053GD | LedGreen | Typical INFRARED GaAs LED | 1581138 |  | LED0
1 | D3 | MCL053MD | LedGreen | Typical INFRARED GaAs LED | 1581137 |  | LED0
1 | D10 | MCL053YD | LedGreen | Typical INFRARED GaAs LED | 1581139 |  | LED0
1 | D12 | BAS316,115 | Didode (Regulator) | Default Diode | 8734275 |  | Diode
1 | FB1 | Comment | Inductor | Inductor |  |  | Inductor
1 | L1 | G5RL-U/-K | Electromagnet | Magnetic-Core Inductor | 2432865 |  | Inductor Iron
1 | L2 | 39uH | Inductor (regulator) | Inductor | 2082620 |  | Inductor
1 | LS1 | ABT-414-RC | Buzzer | Header, 2-Pin |  |  | Header 2
2 | M1, M2 | MG-6-120 | Motor2 | Motor, General Kind |  | MG-6-120 | Motor
1 | P1 | JST5 | LDR_RGB | Header, 5-Pin |  |  | MHDR1X5
1 | P2 | TerminalConnector | TerminalConector | Header, 2-Pin, Right Angle |  |  | Header 2H
1 | PIC32Square | PIC32MX340F256H | PIC32 |  | 1523322 |  | PIC32square
1 | PROG | 22-29-2061 | HEADER-6-PIN |  |  |  | HEADER-6-PIN
8 | Q1, Q2, Q3, Q4, Q5, Q6, Q7, Q8 | 2N7002 | Mosfet | N-Channel MOSFET | 2775064 |  | MOSFET-N
2 | Q9, Q10 | 2N7002-G | Mosfet | N-Channel MOSFET | 2775064 |  | MOSFET-N
16 | R1, R2, R3, R4, R5, R6, R7, R8, R9, R10, R11, R12, R13, R14, R15, R16 | 10 K | Resistor0603 | Resistor |  |  | Res1
1 | R17 | 1K | Resistor0603 | Resistor |  |  | Res1
1 | R18 | 87 Ohm | Resistor0603 | Resistor |  |  | Res1
2 | R19, R20 | 20 Ohm | Resistor0603 | Resistor |  |  | Res1
2 | R21, R22 | 5 KOhm | Resistor0603 | Resistor |  |  | Res1
12 | R23, R24, R25, R26, R27, R28, R29, R30, R31, R33, R34, R35 | 80 Ohm | Resistor0603 | Resistor |  |  | Res1
1 | R32 | 93 Ohm | Resistor0603 | Resistor |  |  | Res1
1 | R36 | 10K | Resistor0603 | Resistor |  |  | Res1
1 | R38 | 1 KOhm | Resistor0603 | Resistor |  |  | Res1
1 | R39 | 3.32 KOhm | Resistor0603 | Resistor |  |  | Res1
1 | R40 | 470 Ohm | Resistor0603 | Resistor |  |  | Res1
1 | REGULATOR | LMR14203X | REGULATOR |  | 2064680 |  | Regulator
16 | R_VAR1, R_VAR2, R_VAR3, R_VAR4, R_VAR5, R_VAR6, R_VAR7, R_VAR8, R_VAR9, R_VAR10, R_VAR11, R_VAR12, R_VAR13, R_VAR14, R_VAR15, R_VAR16 | 1.5K ~ 100K | OrderPiece | Resistor |  |  | Res1
2 | S1, S3 | SS12SDP2 | Switch | Single-Pole, Single-Throw Switch | 1524325 |  | SW-SPST
1 | S2 | R13-509A-05-BB | StartButton | Switch | 1634682 |  | SW-PB
2 | U2, U8 | 74HC164 | SHIFT REGISTER |  | 1103161 |  | Shift Register
1 | U3 | TC23-11GWA | LEDPANEL |  | 2290396 |  | LED Dot Matrix
1 | U4 | CD74HC4067SM96 | MUX |  | 1601157 |  | Analog Multiplexor
1 | U5 | GP2Y0A41SK0F | Proximity2 |  | 1618431 |  | Proximity sensor
1 | U6 | L293DNE | MotorDriver |  | 1470423 |  | Motor Driver
1 | U7 | RN4020 | bluetooth |  | 2442930 |  | Blueetooth

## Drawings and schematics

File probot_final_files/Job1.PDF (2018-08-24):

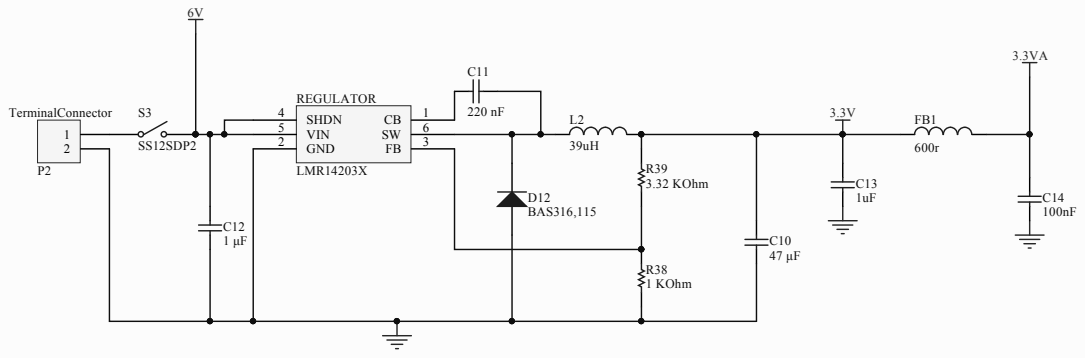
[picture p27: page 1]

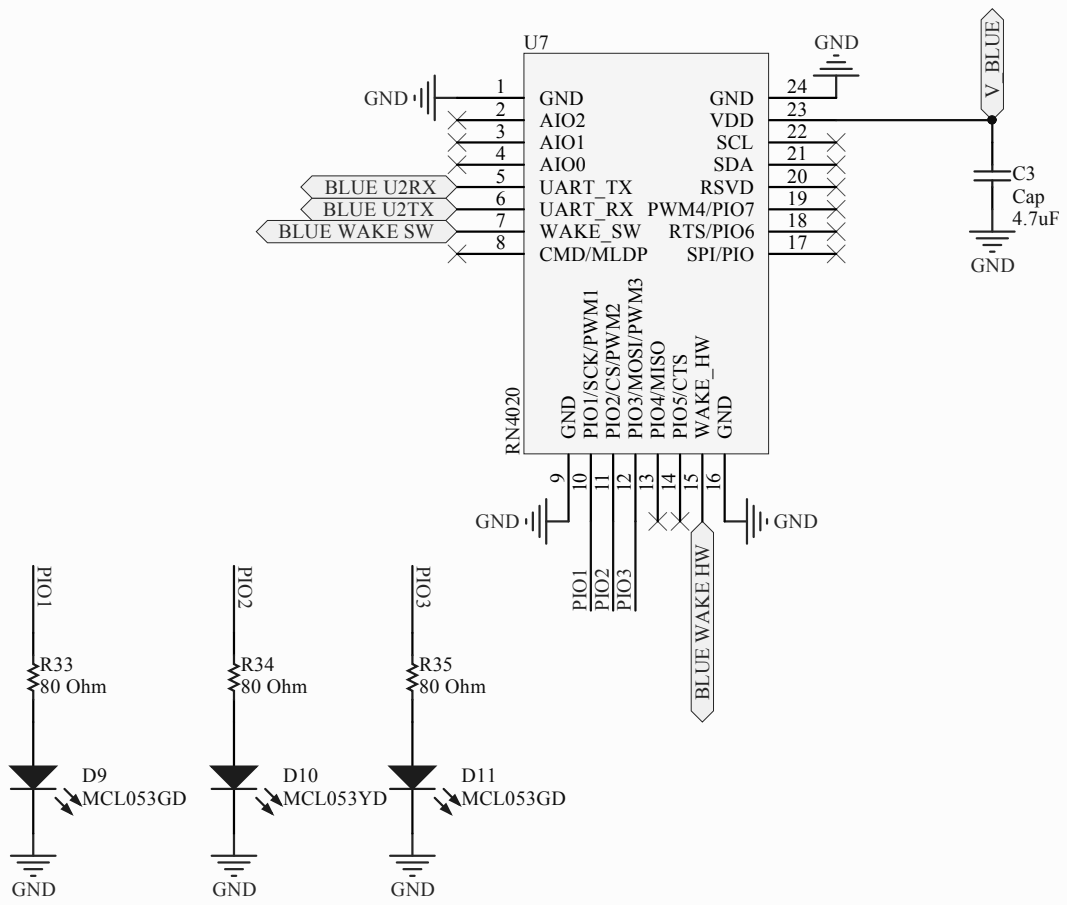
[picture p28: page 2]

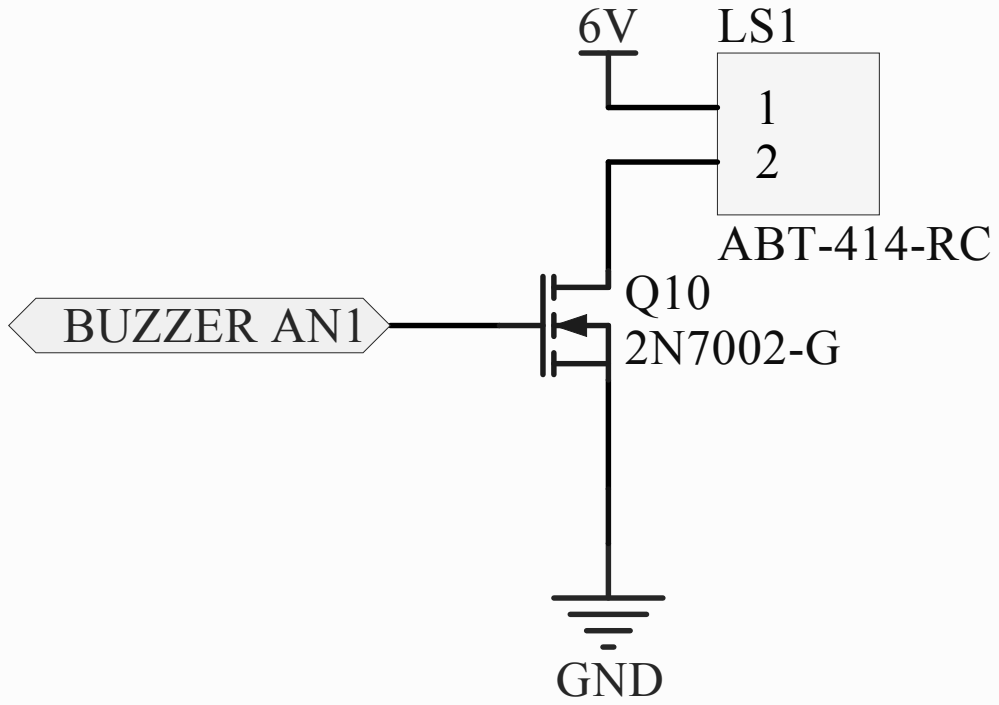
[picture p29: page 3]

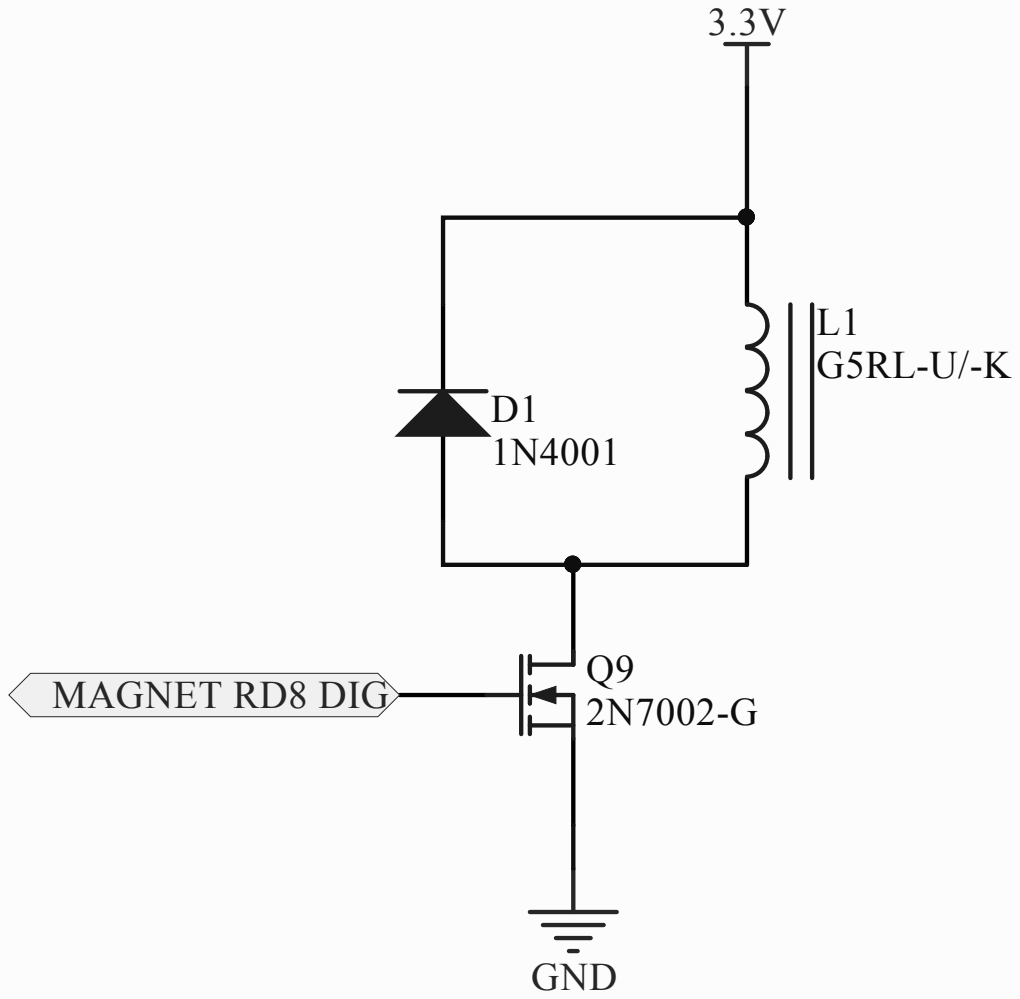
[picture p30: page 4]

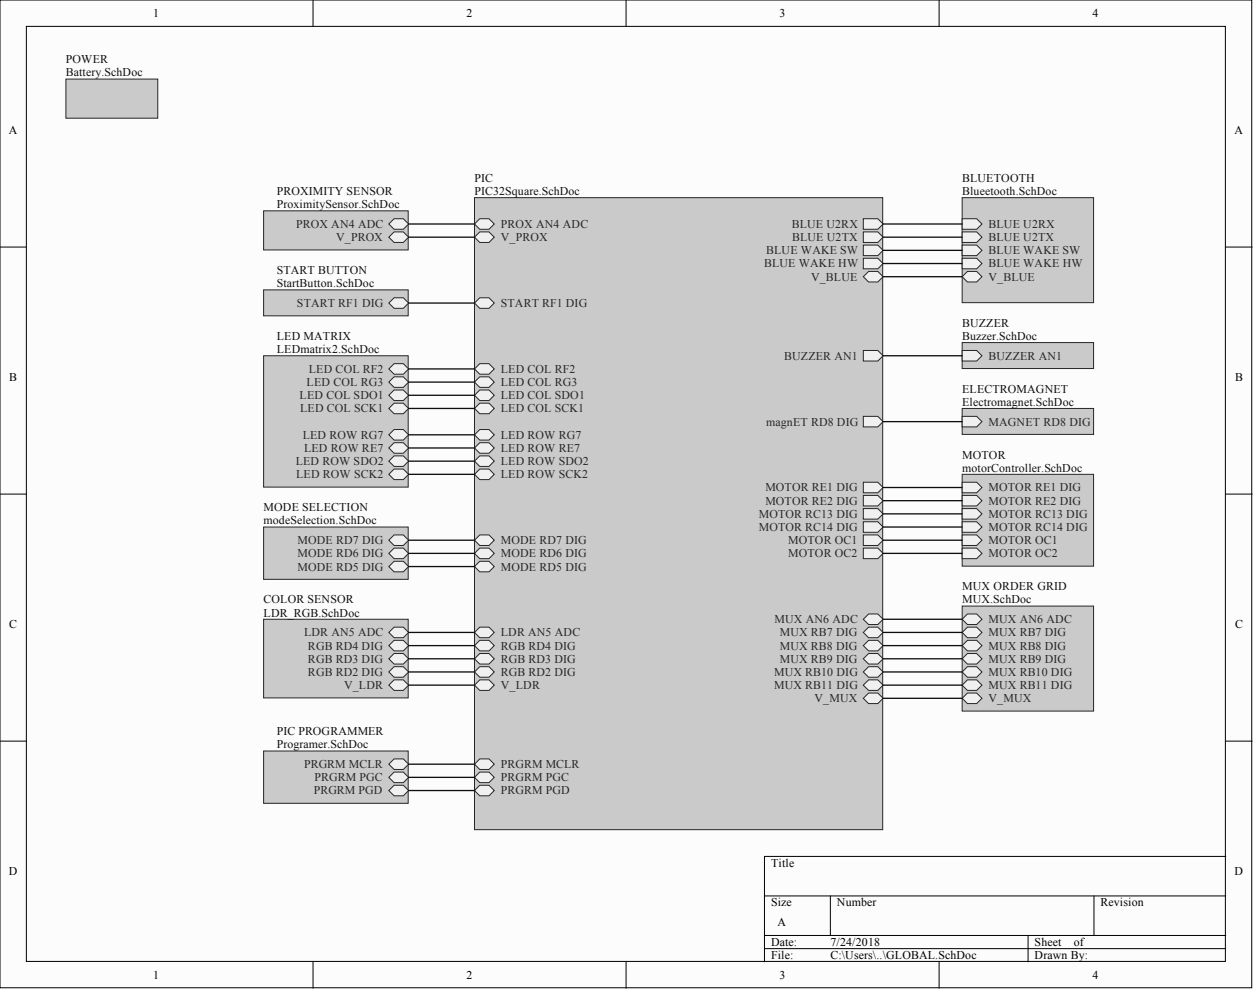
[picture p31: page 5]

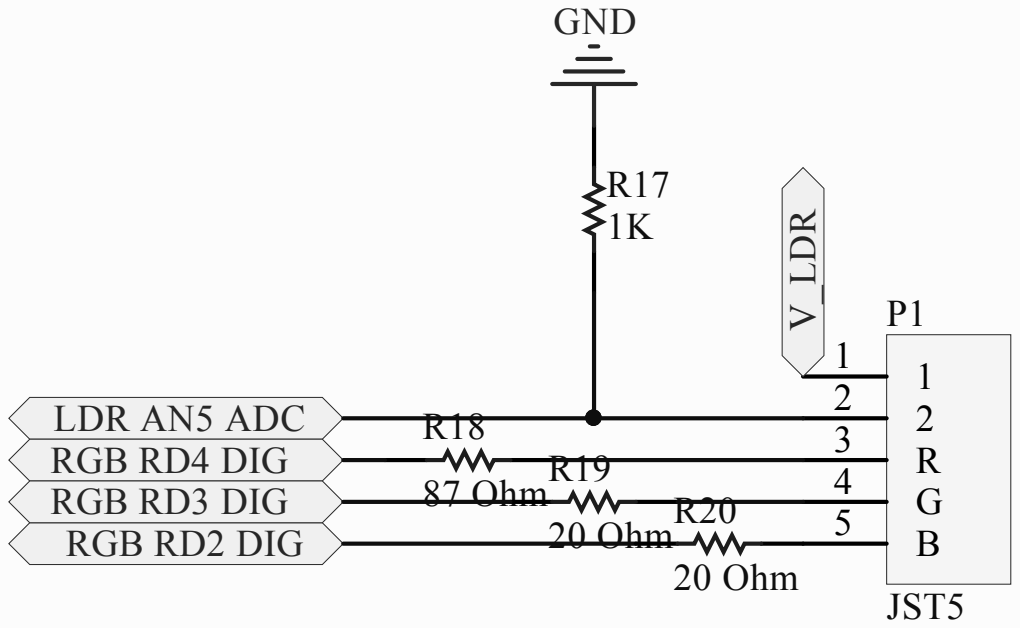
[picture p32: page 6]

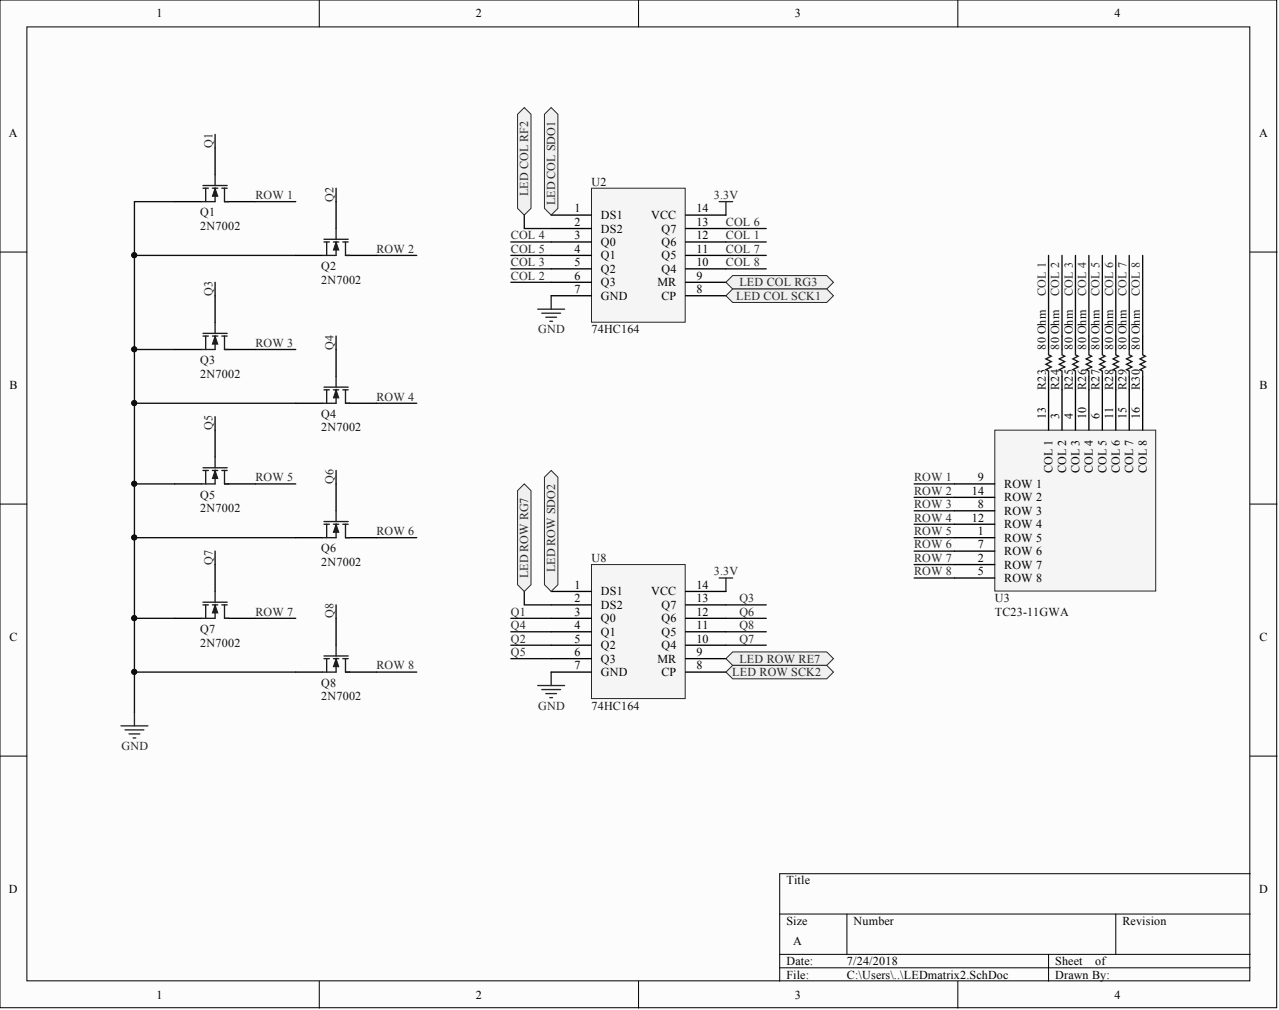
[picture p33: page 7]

COL 8 16 COL 7 15 COL 6 11 COL 5 6 COL 4 10 COL 3 4 COL 2 3 COL 1 13

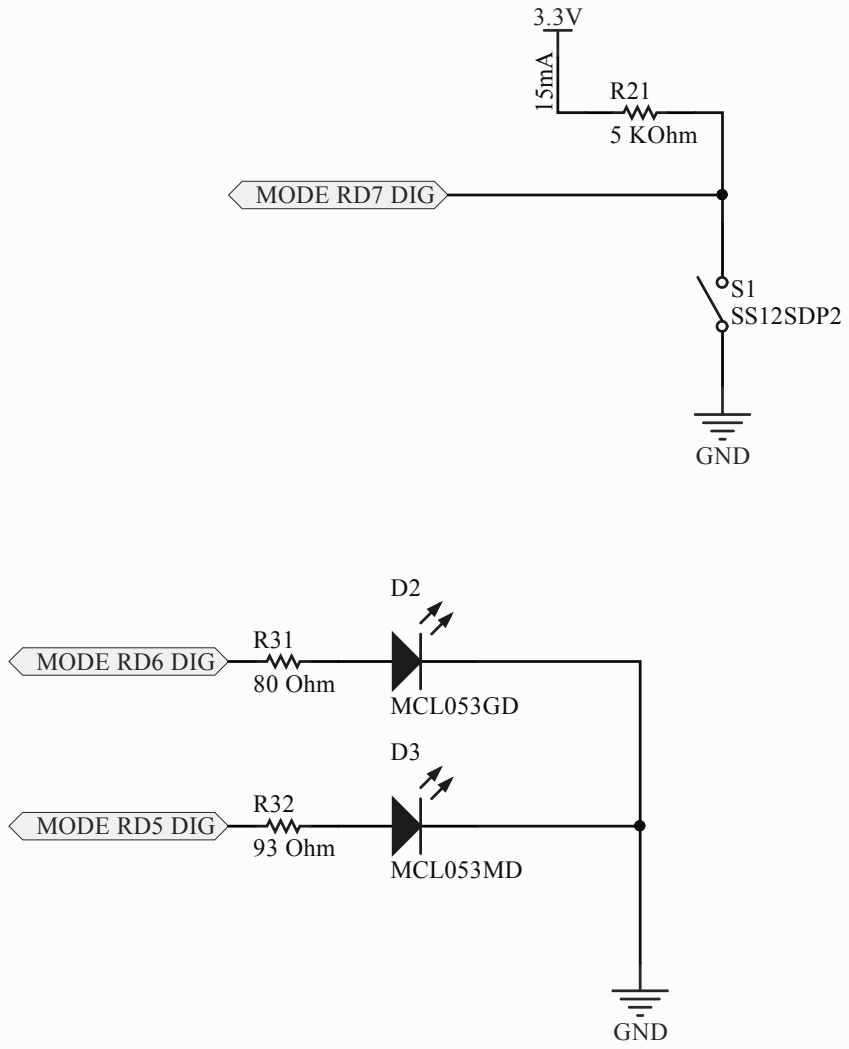
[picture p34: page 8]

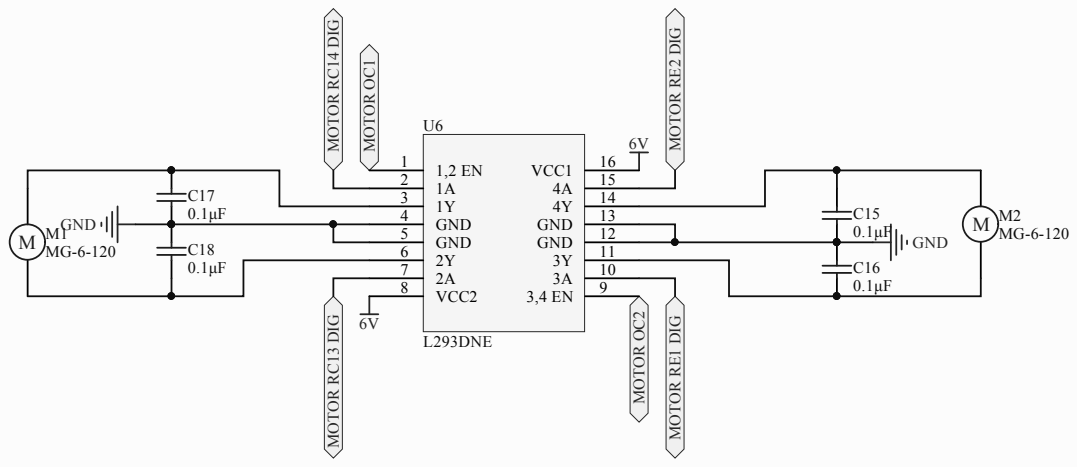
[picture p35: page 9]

MOTOR RC14 DIG MOTOR RC13 DIG

MOTOR RE1 DIG MOTOR RE2 DIG

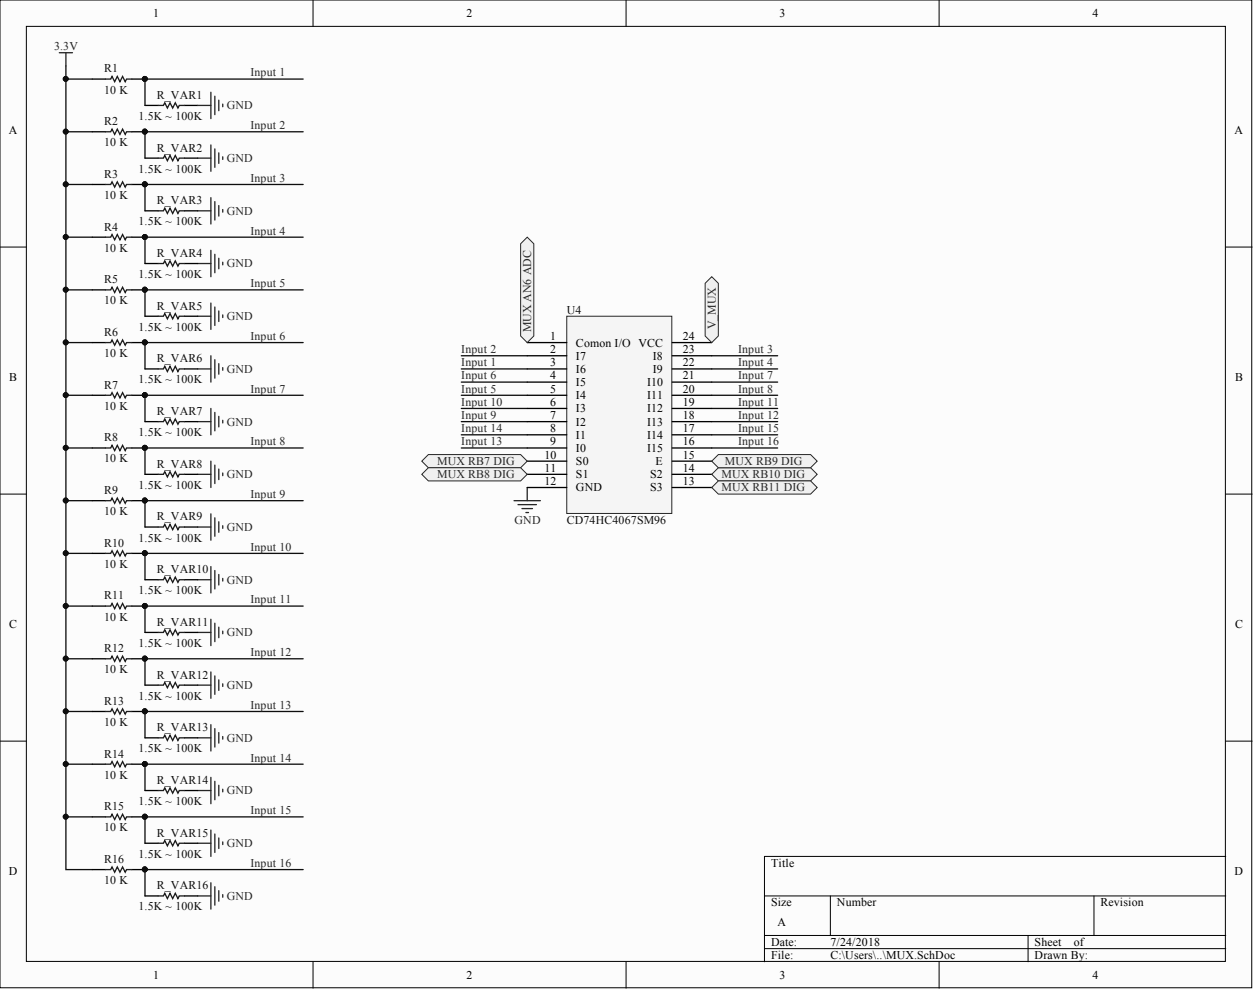
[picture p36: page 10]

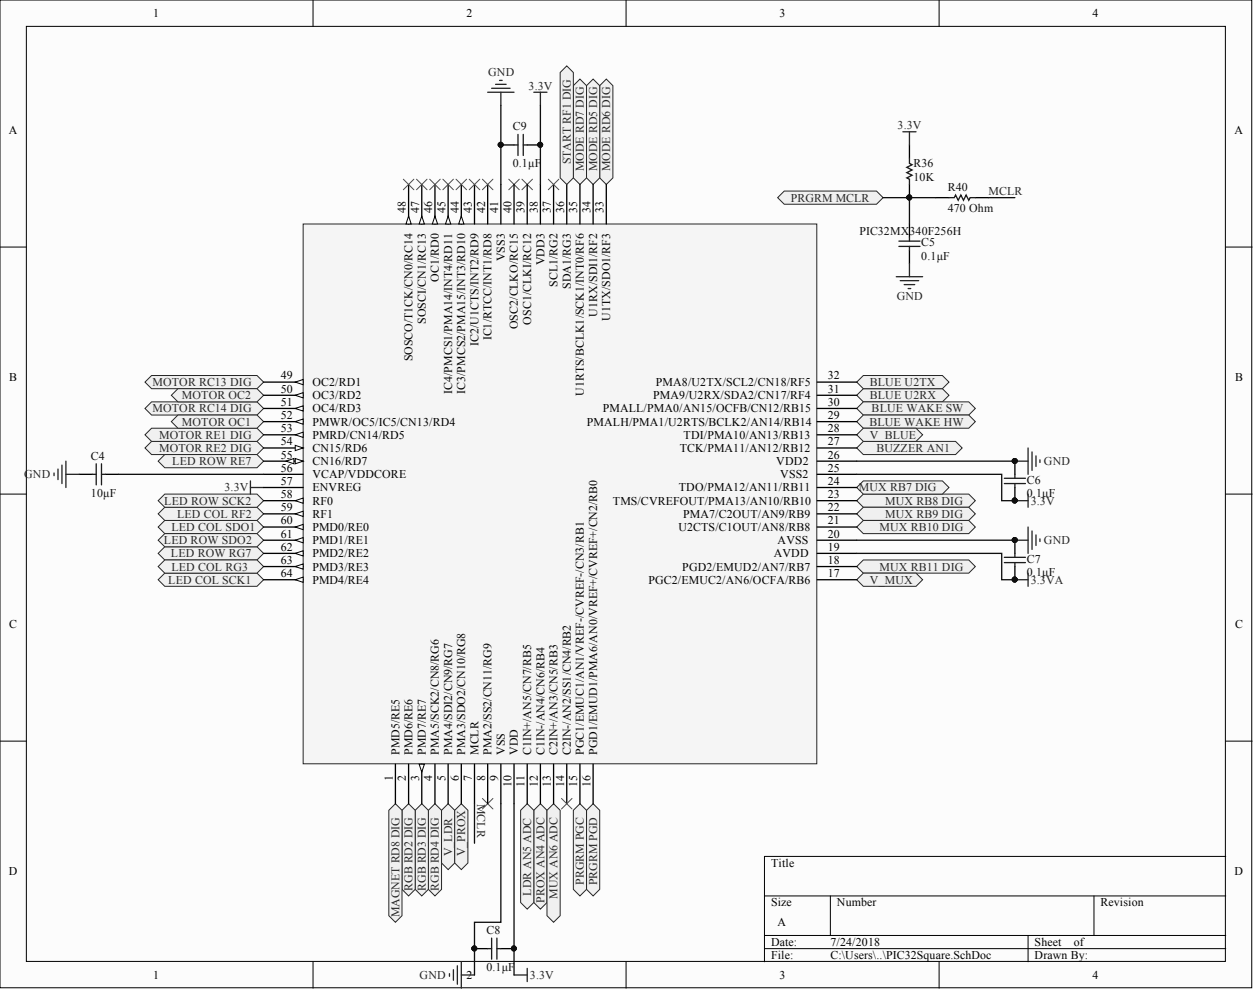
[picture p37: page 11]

U1RX/SDI1/RF2 34 U1RTS/BCLK1/SCK1/INT0/RF6 35 SDA1/RG3 36 SCL1/RG2 37 VDD3 38 OSC1/CLKI/RC12 39 OSC2/CLKO/RC15 40 VSS3 41 IC1/RTCC/INT1/RD8 42 IC2/U1CTS/INT2/RD9 43 IC3/PMCS2/PM

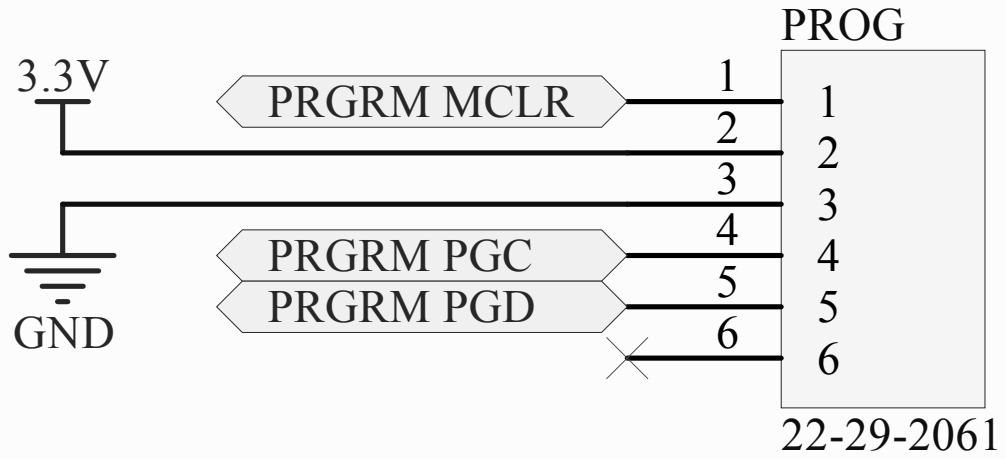
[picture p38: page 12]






Quantity | Designator | Comment | Footprint | Description | Farnell Reference | Olimex Reference | LibRef
1 | C3 | Cap | Capacitor | Capacitor | | | Cap
1 | C4 | 10µF | Capacitor | Capacitor | | | Cap
| C5, C6, C7, C8, C9, C15, C16, C17, C18 | 0.1µF | Capacitor | Capacitor | | | Cap
1 | C10 | 47 µF | Capacitor | Capacitor | | | Cap
1 | C11 | 220 nF | Capacitor | Capacitor | | | Cap
1 | C12 | 1 µF | Capacitor | Capacitor | | | Cap
1 | C13 | 1uF | Capacitor | Capacitor | | | Cap
1 | C14 | 100nF | Capacitor | Capacitor | | | Cap
1 | D1 | 1N4001 | Diode | Default Diode | 9564993 | | Diode
3 | D2, D9, D11 | MCL053GD | LedGreen | Typical INFRARED GaAs LED | 1581138 | | LED0
1 | D3 | MCL053MD | LedGreen | Typical INFRARED GaAs LED | 1581137 | | LED0
1 | D10 | MCL053YD | LedGreen | Typical INFRARED GaAs LED | 1581139 | | LED0
1 | D12 | BAS316,115 | Didode (Regulator) | Default Diode | 8734275 | | Diode
1 | FB1 | Comment | Inductor | Inductor | | | Inductor
1 | L1 | G5RL-U/-K | Electromagnet | Magnetic-Core Inductor | 2432865 | | Inductor Iron
1 | L2 | 39uH | Inductor (regulator) | Inductor | 2082620 | | Inductor
1 | LS1 | ABT-414-RC | Buzzer | Header, 2-Pin | | | Header 2
2 | M1, M2 | MG-6-120 | Motor2 | Motor, General Kind | | MG-6-120 | Motor
1 | P1 | JST5 | LDR_RGB | Header, 5-Pin | | | MHDR1X5
1 | P2 | TerminalConnect or | TerminalConecto r | Header, 2-Pin, Right Angle | | | Header 2H
1 | PIC32Square | PIC32MX340F256 H | PIC32 | | 1523322 | | PIC32square
1 | PROG | 22-29-2061 | HEADER-6-PIN | | | | HEADER-6-PIN
8 | Q1, Q2, Q3, Q4, Q5, Q6, Q7, Q8 | 2N7002 | Mosfet | N-Channel MOSFET | 2775064 | | MOSFET-N
2 | Q9, Q10 | 2N7002-G | Mosfet | N-Channel MOSFET | 2775064 | | MOSFET-N
16 | R1, R2, R3, R4, R5, R6, R7, R8, R9, R10, R11, R12, R13, R14, R15, R16 | 10 K | Resistor0603 | Resistor | | | Res1
1 | R17 | 1K | Resistor0603 | Resistor | | | Res1
1 | R18 | 87 Ohm | Resistor0603 | Resistor | | | Res1
2 | R19, R20 | 20 Ohm | Resistor0603 | Resistor | | | Res1
2 | R21, R22 | 5 KOhm | Resistor0603 | Resistor | | | Res1
12 | R23, R24, R25, R26, R27, R28, R29, R30, R31, R33, R34, R35 | 80 Ohm | Resistor0603 | Resistor | | | Res1
1 | R32 | 93 Ohm | Resistor0603 | Resistor | | | Res1
1 | R36 | 10K | Resistor0603 | Resistor | | | Res1
1 | R38 | 1 KOhm | Resistor0603 | Resistor | | | Res1
1 | R39 | 3.32 KOhm | Resistor0603 | Resistor | | | Res1
1 | R40 | 470 Ohm | Resistor0603 | Resistor | | | Res1
1 | REGULATOR | LMR14203X | REGULATOR | | 2064680 | | Regulator
16 | R_VAR1, R_VAR2, R_VAR3, R_VAR4, R_VAR5, R_VAR6, R_VAR7, R_VAR8, R_VAR9, R_VAR10, R_VAR11, R_VAR12, R_VAR13, R_VAR14, R_VAR15, R_VAR16 | 1.5K ~ 100K | OrderPiece | Resistor | | | Res1
2 | S1, S3 | SS12SDP2 | Switch | Single-Pole, Single-Throw Switch | 1524325 | | SW-SPST
1 | S2 | R13-509A-05-BB | StartButton | Switch | 1634682 | | SW-PB
2 | U2, U8 | 74HC164 | SHIFT REGISTER | | 1103161 | | Shift Register
1 | U3 | TC23-11GWA | LEDPANEL | | 2290396 | | LED Dot Matrix
1 | U4 | CD74HC4067SM9 6 | MUX | | 1601157 | | Analog Multiplexor
1 | U5 | GP2Y0A41SK0F | Proximity2 | | 1618431 | | Proximity sensor
1 | U6 | L293DNE | MotorDriver | | 1470423 | | Motor Driver
1 | U7 | RN4020 | bluetooth | | 2442930 | | Blueetooth

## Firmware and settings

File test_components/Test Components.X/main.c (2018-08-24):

#include "Type.h"
#include "p32xxxx.h"
#include <sys/attribs.h>

static void	test_pins(void)
{
	TRISEbits.TRISE2 = 0;
	TRISEbits.TRISE3 = 0;
	TRISEbits.TRISE4 = 0;
	TRISEbits.TRISE5 = 0;

	LATEbits.LATE2 = 1;
	LATEbits.LATE3 = 1;
	LATEbits.LATE4 = 1;
	LATEbits.LATE5 = 1;

}
int main(void)
{
	u16 start;
//	conf_file.c
//	test_proximity_sensor();
//    test_mux2();
//	motor_driver();
	mux_final();
//	while (1)
//	{
//		start = start_button(); //MANEJAR EL START_BUTTON COMO UNA INTERRUPCION
//		if (start_button)
//			test_mux2();
//	}
//    return (0);
}

//TODO
//
//1 CREAR ORDER PIECES
//2 SENSOR CON INTERRUPCIONS
//3 CREAR DIBUJOS EN LED PANEL --> | <-- | ... | :) | :( | X( |
//
//

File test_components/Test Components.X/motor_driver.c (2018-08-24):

#include "Type.h"
#include "p32xxxx.h"
#include <sys/attribs.h>

//https://www.rakeshmondal.info/dc-motor-control-introhttps://www.rakeshmondal.info/dc-motor-control-intro

static void	set_motors(void)
{
	//MOTOR 1 output
	TRISFbits.TRISF2 = 0;
	TRISFbits.TRISF3 = 0;
	//MOTOR 2 output
	TRISFbits.TRISF4 = 0;
	TRISFbits.TRISF5 = 0;

	LATFbits.LATF2 = 0;
	LATFbits.LATF3 = 0;
	LATFbits.LATF4 = 0;
	LATFbits.LATF5 = 0;
}
static void stop_motor(void)
{
	LATFbits.LATF2 = 0;
	LATFbits.LATF3 = 0;
	LATFbits.LATF4 = 0;
	LATFbits.LATF5 = 0;
}
static void	go_forward(void)
{
	//INTERRUPTIONS{ meterlo en una funcion
	 //TIMER va desde TMR2 a PR2
    PR2 = 62500;
    TMR2 = 0;
    T2CONbits.ON = 1;       //Encender clock
    T2CONbits.TCKPS = 0b100;    //TCKPS<2:0> 011 = 1:8 prescale value
    T2CONbits.TGATE = 0;
    IFS0bits.T2IF = 0;       //T2IF = watchdog, cuando TMR2 = PR2 -> T2IF = 1; [IMPORTANTE DEVOLVER A CERO]
    IEC0bits.T2IE = 1;
    IPC2bits.T2IP = 5;
	//}INTERRUPTIONS//

	LATFbits.LATF1 = 1; //Encender lucecilla
	int i = 1000;
	while(i)
	{
		//MOTOR 1
		LATFbits.LATF2 = 1;
		LATFbits.LATF3 = 0;
		//MOTOR 2
		LATFbits.LATF4 = 1;
		LATFbits.LATF5 = 0;
		i--;
	}
	LATFbits.LATF2 = 0;
	LATFbits.LATF3 = 0;
	LATFbits.LATF4 = 0;
	LATFbits.LATF5 = 0;
}

static void	go_backwards(void)
{
	LATFbits.LATF1 = 1; //Encender lucecilla
	int i = 1000;
	while(i)
	{
		//MOTOR 1
		LATFbits.LATF2 = 0;
		LATFbits.LATF3 = 1;
		//MOTOR 2
		LATFbits.LATF4 = 0;
		LATFbits.LATF5 = 1;
		i--;
	}
	LATFbits.LATF2 = 0;
	LATFbits.LATF3 = 0;
	LATFbits.LATF4 = 0;
	LATFbits.LATF5 = 0;
}

static void	turn_right(void)
{
	LATFbits.LATF1 = 1; //Encender lucecilla
	int i = 1000;
	while(i)
	{
		//MOTOR 1
		LATFbits.LATF2 = 0;
		LATFbits.LATF3 = 1;
		//MOTOR 2
		LATFbits.LATF4 = 1;
		LATFbits.LATF5 = 0;
		i--;
	}
	LATFbits.LATF2 = 0;
	LATFbits.LATF3 = 0;
	LATFbits.LATF4 = 0;
	LATFbits.LATF5 = 0;
}
static void	turn_left(void)
{
	LATFbits.LATF1 = 1; //Encender lucecilla
	int i = 1000;
	while(i)
	{
		//MOTOR 1
		LATFbits.LATF2 = 1;
		LATFbits.LATF3 = 0;
		//MOTOR 2
		LATFbits.LATF4 = 0;
		LATFbits.LATF5 = 1;
		i--;
	}
	LATFbits.LATF2 = 0;
	LATFbits.LATF3 = 0;
	LATFbits.LATF4 = 0;
	LATFbits.LATF5 = 0;
}

void	motor_driver(int direction)
{


	
	TRISFbits.TRISF1 = 0; //Lucecilla output
	set_motors();
	if (direction == 0)
		stop_motor();
	else if (direction == 1)
		go_forward();
	else if (direction == 2)
		go_backwards();
	else if (direction == 3)
		turn_right();
	else if (direction == 4)
		turn_left();
	LATFbits.LATF1 = 0; //Encender lucecilla
}

void __ISR(_TIMER_2_VECTOR, IPL5SRS)TP4InterruptT2(void)
{
	// Reset interrupt flag
    IFS0bits.T2IF = 0;
}
